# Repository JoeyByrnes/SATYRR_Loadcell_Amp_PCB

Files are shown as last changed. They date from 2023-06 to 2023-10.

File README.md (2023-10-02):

# SATYRR Loadcell Amplifier PCB
Loadcell Amplifiers for RoboDesign Lab SATYRR Wheeled-Humanoid robot

<p align="center">
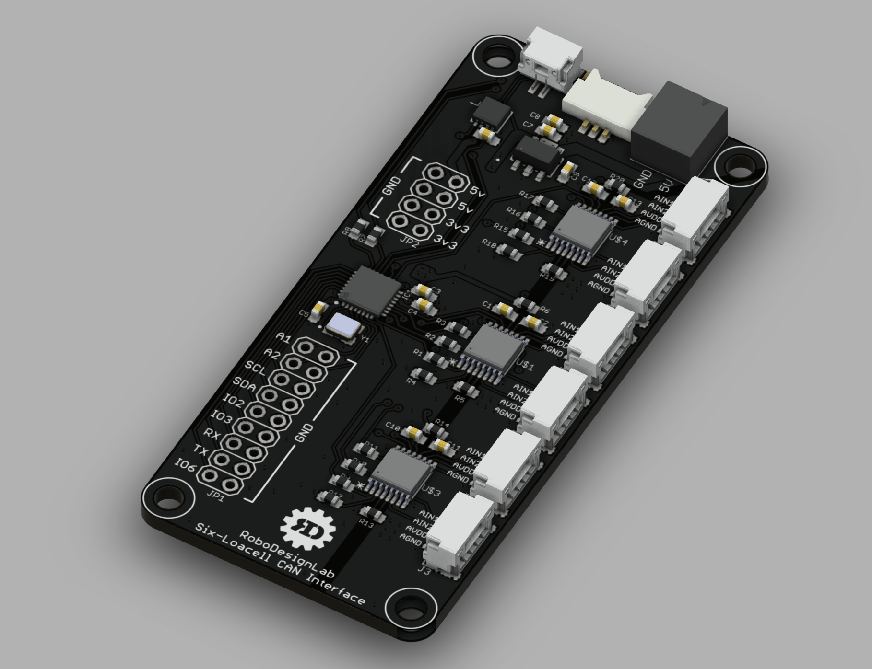
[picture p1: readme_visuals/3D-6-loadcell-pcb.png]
  
</p>

<p align="center">
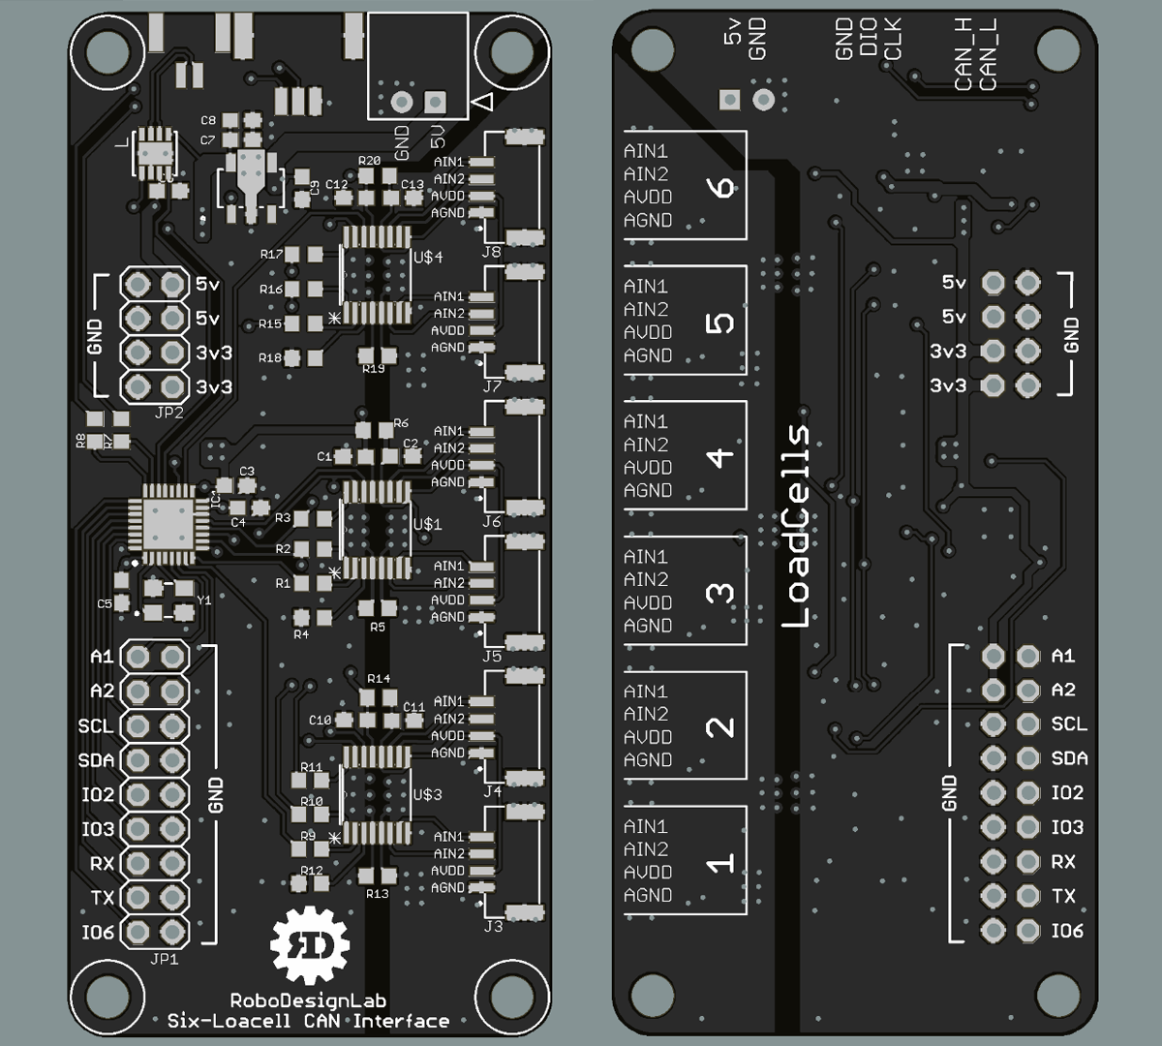
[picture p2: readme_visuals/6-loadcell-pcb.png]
  
</p>

<p align="center">
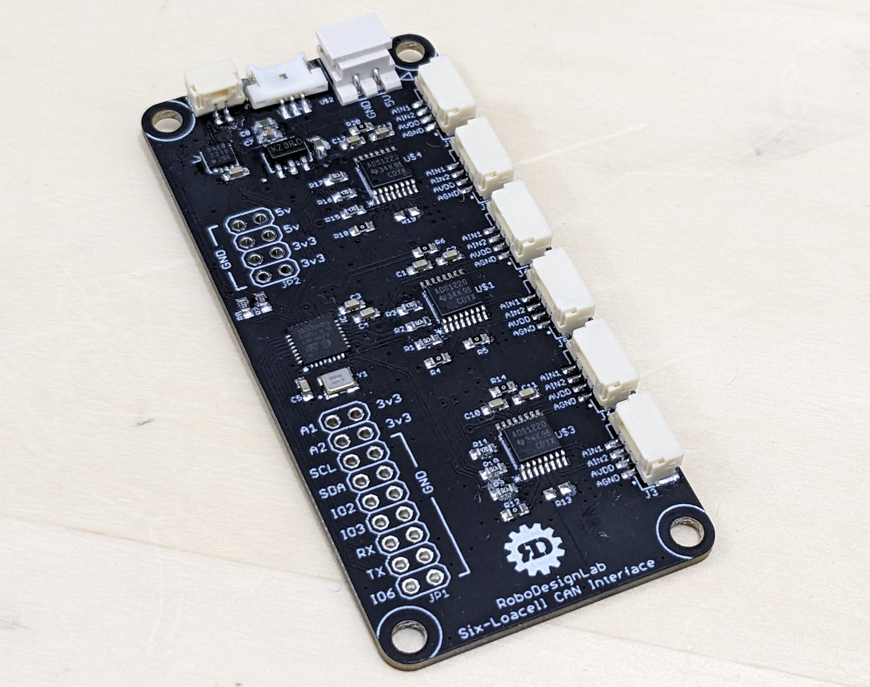
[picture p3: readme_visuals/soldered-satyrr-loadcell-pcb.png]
  
</p>

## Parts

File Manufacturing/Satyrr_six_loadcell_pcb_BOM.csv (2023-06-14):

Qty | Value | Package | Parts | Links
9 | 0R | R0603 | R4 R5 R6 R12 R13 R14 R18 R19 R20 | https://www.digikey.com/en/products/detail/stackpole-electronics-inc/RMCF0603ZT0R00/1756908
10 | 0.1uF | C0603 | C1 C2 C10 C11 C12 C13 C3 C4 C5 C6 | https://www.digikey.com/en/products/detail/samsung-electro-mechanics/CL10B104KB8NNWC/3887593
2 | 10uF | C0603 | C8 C9 | https://www.digikey.com/en/products/detail/taiyo-yuden/LMK107BBJ106MALT/3662195
1 | 125SH-G-03-TR-SMT | 125SH-G-03-TR-SMT | U$2 | https://www.digikey.com/en/products/detail/adam-tech/125SH-G-03-TR-SMT-T-R/10414814
1 | 22057025 | CON_22057025_MOL | J9 | https://www.digikey.com/en/products/detail/molex/0022057025/403341?s=N4IgTCBcDa5gDAVgOzzIkBdAvkA
2 | 22R | R0603 | R7 R8 | https://www.digikey.com/en/products/detail/te-connectivity-passive-product/CRGCQ0603J22R/8576683
1 | 4.7uF | C0603 | C7 | https://www.digikey.com/en/products/detail/taiyo-yuden/LMK107BJ475KAHT/4157765
9 | 47R | R0603 | R1 R2 R3 R9 R10 R11 R15 R16 R17 | https://www.digikey.com/en/products/detail/walsin-technology-corporation/WR06X470-JTL/13241762
3 | ADS1220 | TSSOP-16 | U$1 U$3 U$4 | https://www.mouser.com/ProductDetail/Texas-Instruments/ADS1220IPW?qs=5GI1giJCN%252BKzuruuF2dUlQ%3D%3D
1 | AP7361C-33Y5-13SOT89-5_DIO-M | SOT89-5_DIO-M | U2 | https://www.digikey.com/en/products/detail/diodes-incorporated/AP7361C-33Y5-13/5638323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
1 | ECS-80-18-33-JGN-TR | XTAL_ECS-240-8-33-AGN-TR | Y1 | https://www.digikey.com/en/products/detail/ecs-inc/ECS-80-18-33-JGN-TR/10478755
1 | MCP2562FD-H/MFDFN8_3X3MC_MCH-M | DFN8_3X3MC_MCH-M | U1 | https://www.newark.com/microchip/mcp2562fd-h-sn/can-transceiver-8mbps-40-to-150deg/dp/72AC6153?CMP=AFC-OP
1 | SM02BGHSTBLFSN | CONN_SM02BGHSTB_JST | J2 | https://www.digikey.com/en/products/detail/jst-sales-america-inc/SM02B-GHS-TB-LF-SN/807786
6 | SM04B-GHS-TB(LF)(SN)- | JST_SM04B-GHS-TB(LF)(SN)- | J3 J4 J5 J6 J7 J8 | https://www.digikey.com/en/products/detail/jst-sales-america-inc/SM04B-GHS-TB-LF-SN/807788
1 | STM32G431KBU6 | QFN50P500X500X60-33N | IC1 | https://www.digikey.com/en/products/detail/stmicroelectronics/STM32G431KBU6/10231568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

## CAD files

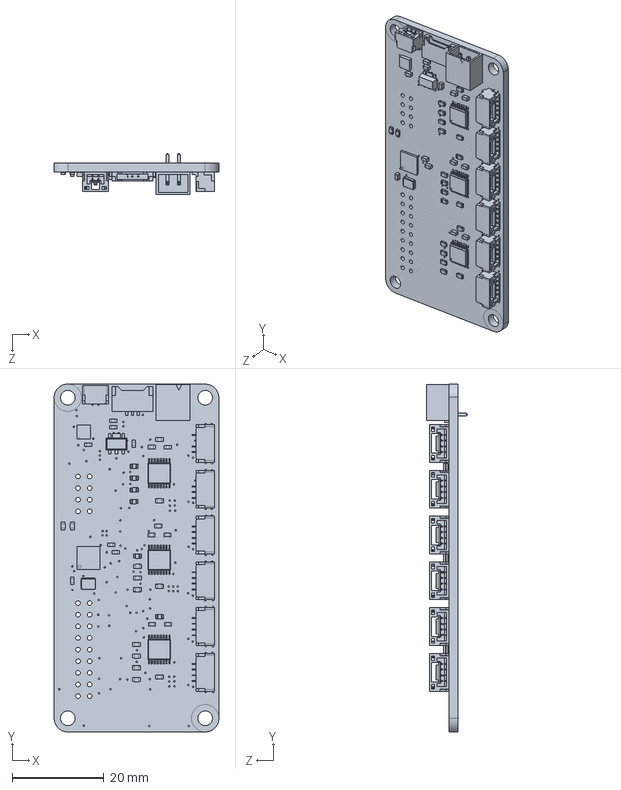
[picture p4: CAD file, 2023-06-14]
3D/Satyrr_6_loadcell_PCB.SLDPRT
36.0 x 76.0 x 9.00 mm

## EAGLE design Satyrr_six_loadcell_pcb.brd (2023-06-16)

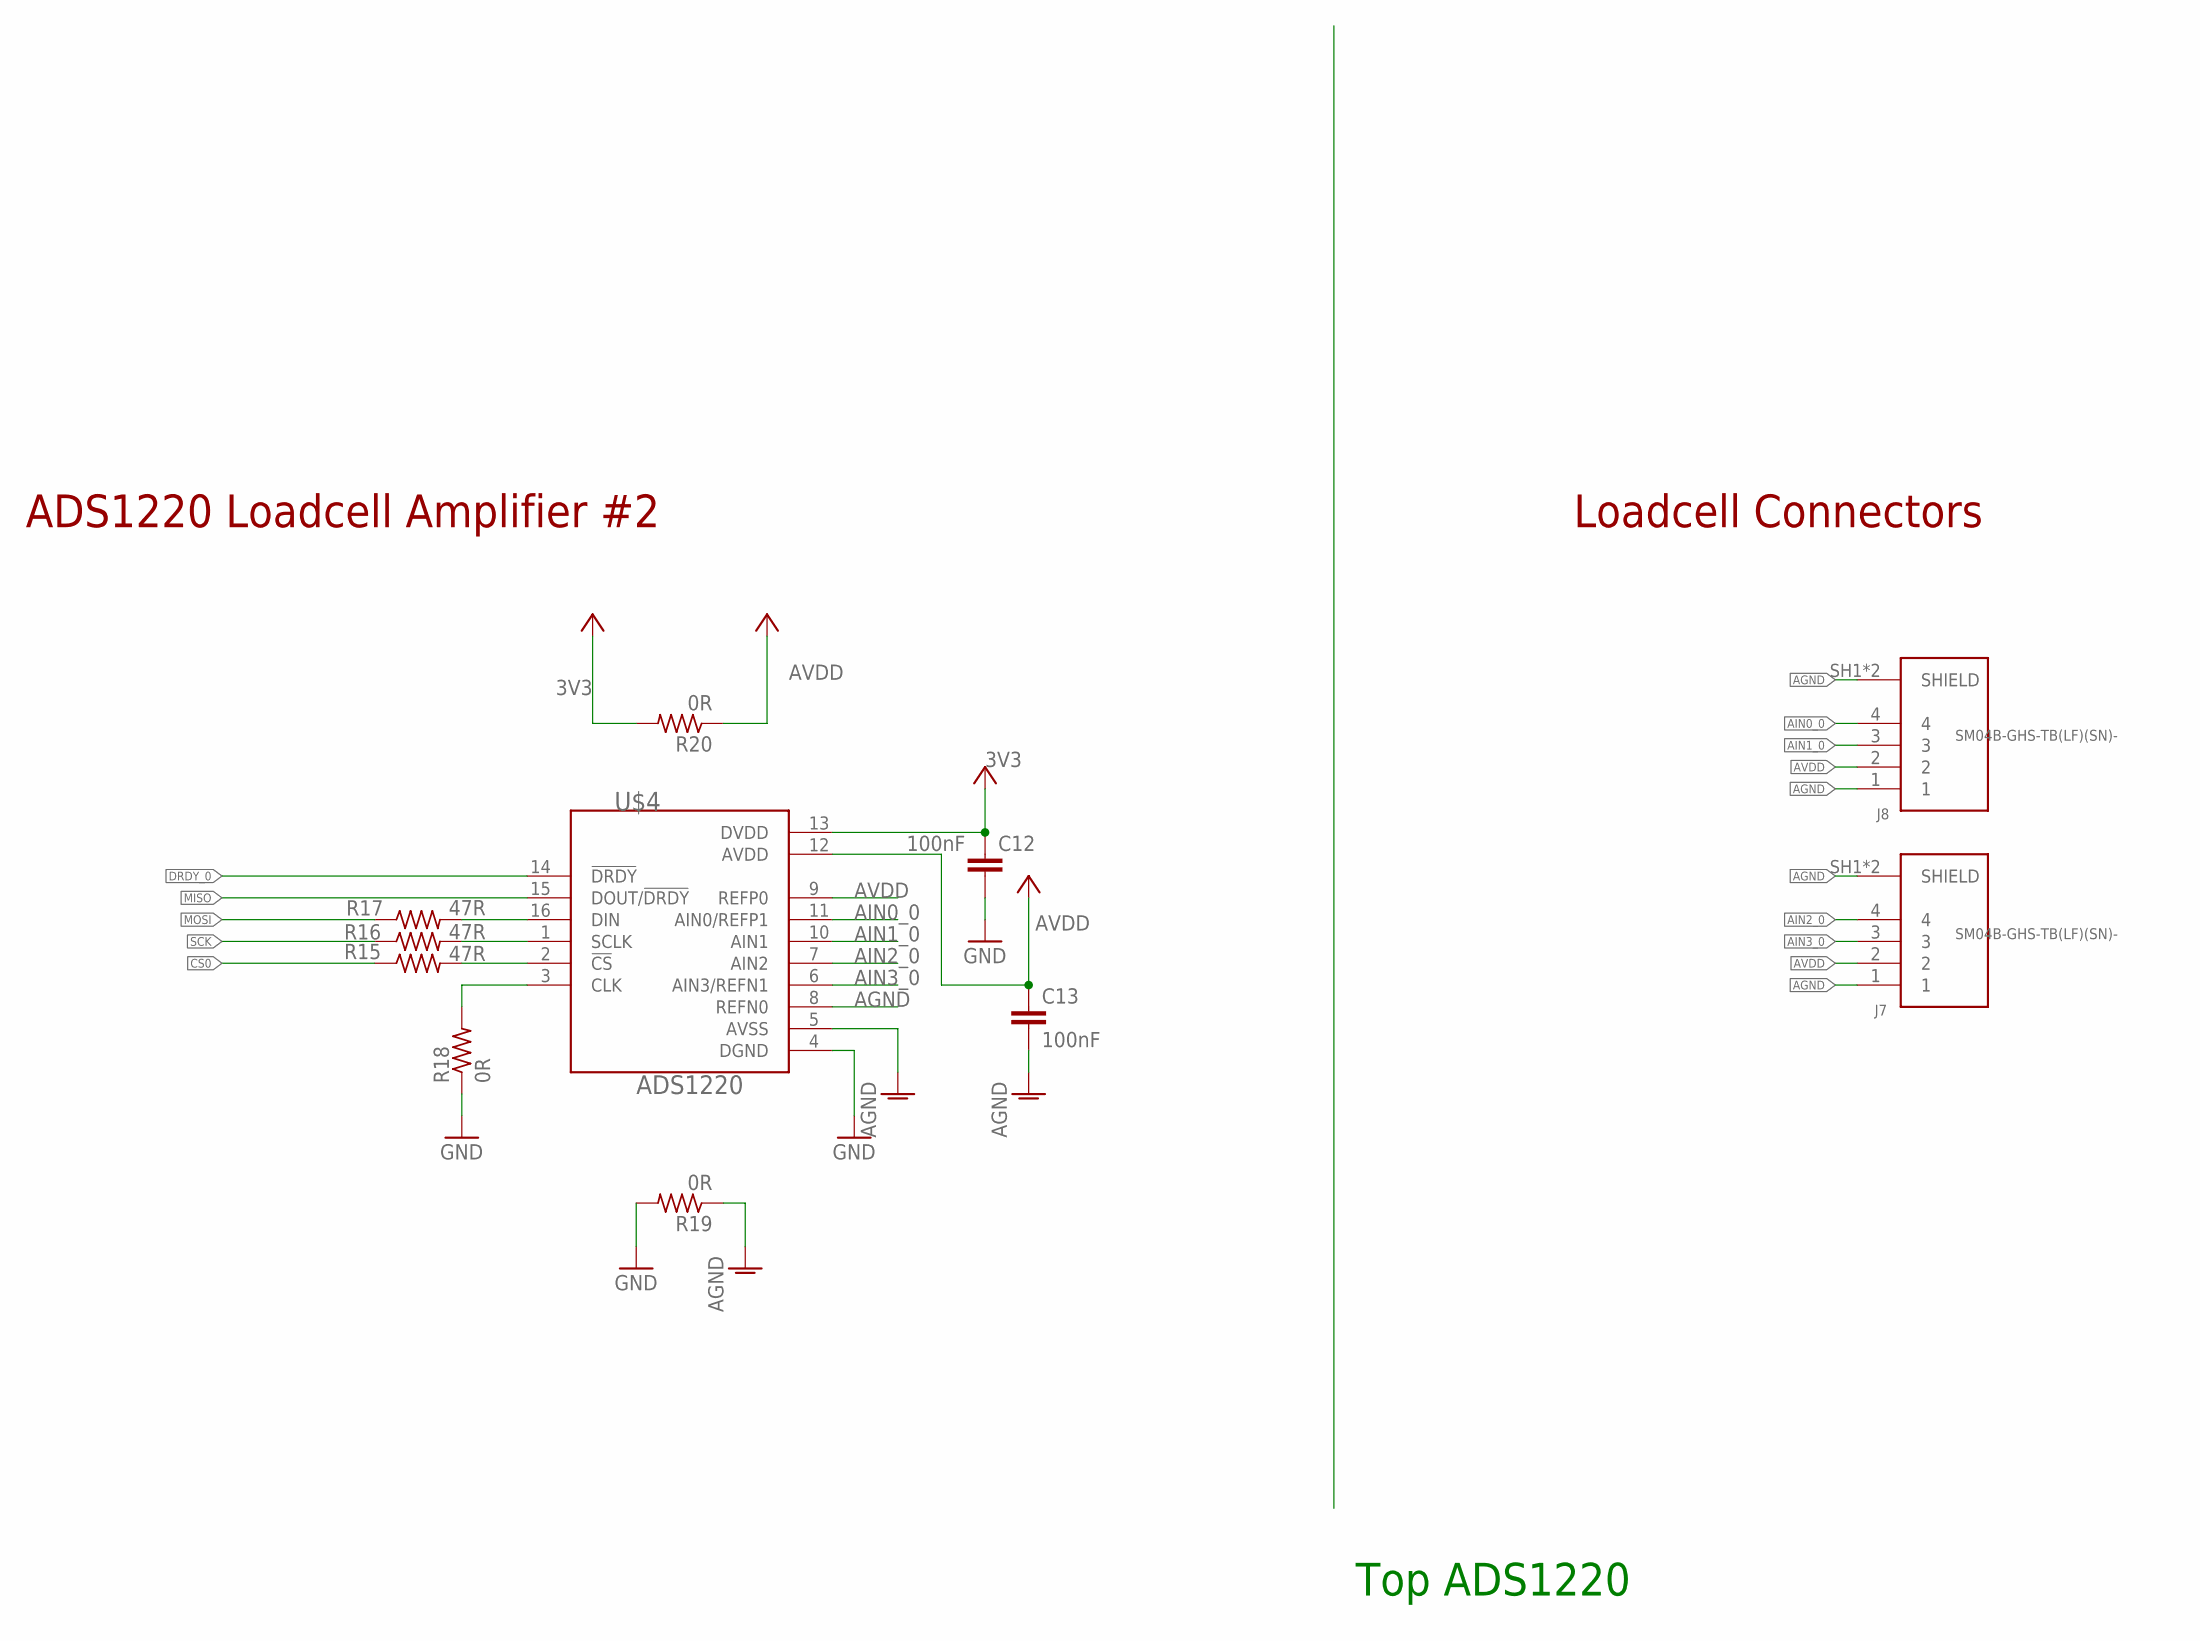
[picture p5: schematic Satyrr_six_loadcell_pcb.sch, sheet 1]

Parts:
C12, C13: 100nF; C0603
J7, J8: SM04B-GHS-TB(LF)(SN)-; JST_SM04B-GHS-TB(LF)(SN)-
R15, R16, R17: 47R; R0603
R18, R19, R20: 0R; R0603
U$4: ADS1220; TSSOP-16

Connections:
3V3: C12.1, R20.2, U$4.13 (DVDD); also elsewhere on the board
AGND: C13.2, J7.1, J7.SH1 (SHIELD), J7.SH2 (SHIELD), J8.1, J8.SH1 (SHIELD), J8.SH2 (SHIELD), R19.1, U$4.5 (AVSS), U$4.8 (REFN0); also elsewhere on the board
AIN0_0: J8.4, U$4.11 (AIN0/REFP1)
AIN1_0: J8.3, U$4.10 (AIN1)
AIN2_0: J7.4, U$4.7 (AIN2)
AIN3_0: J7.3, U$4.6 (AIN3/REFN1)
AVDD: C13.1, J7.2, J8.2, R20.1, U$4.9 (REFP0), U$4.12 (AVDD); also elsewhere on the board
CS0: R15.1; also elsewhere on the board
DRDY_0: U$4.14 (!DRDY); also elsewhere on the board
GND: C12.2, R18.1, R19.2, U$4.4 (DGND); also elsewhere on the board
MISO: U$4.15 (DOUT/!DRDY); also elsewhere on the board
MOSI: R17.1; also elsewhere on the board
unnamed: R17.2, U$4.16 (DIN)
unnamed: R16.2, U$4.1 (SCLK)
unnamed: R15.2, U$4.2 (!CS)
unnamed: R18.2, U$4.3 (CLK)
SCK: R16.1; also elsewhere on the board

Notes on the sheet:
Top ADS1220
ADS1220 Loadcell Amplifier #2
Loadcell Connectors

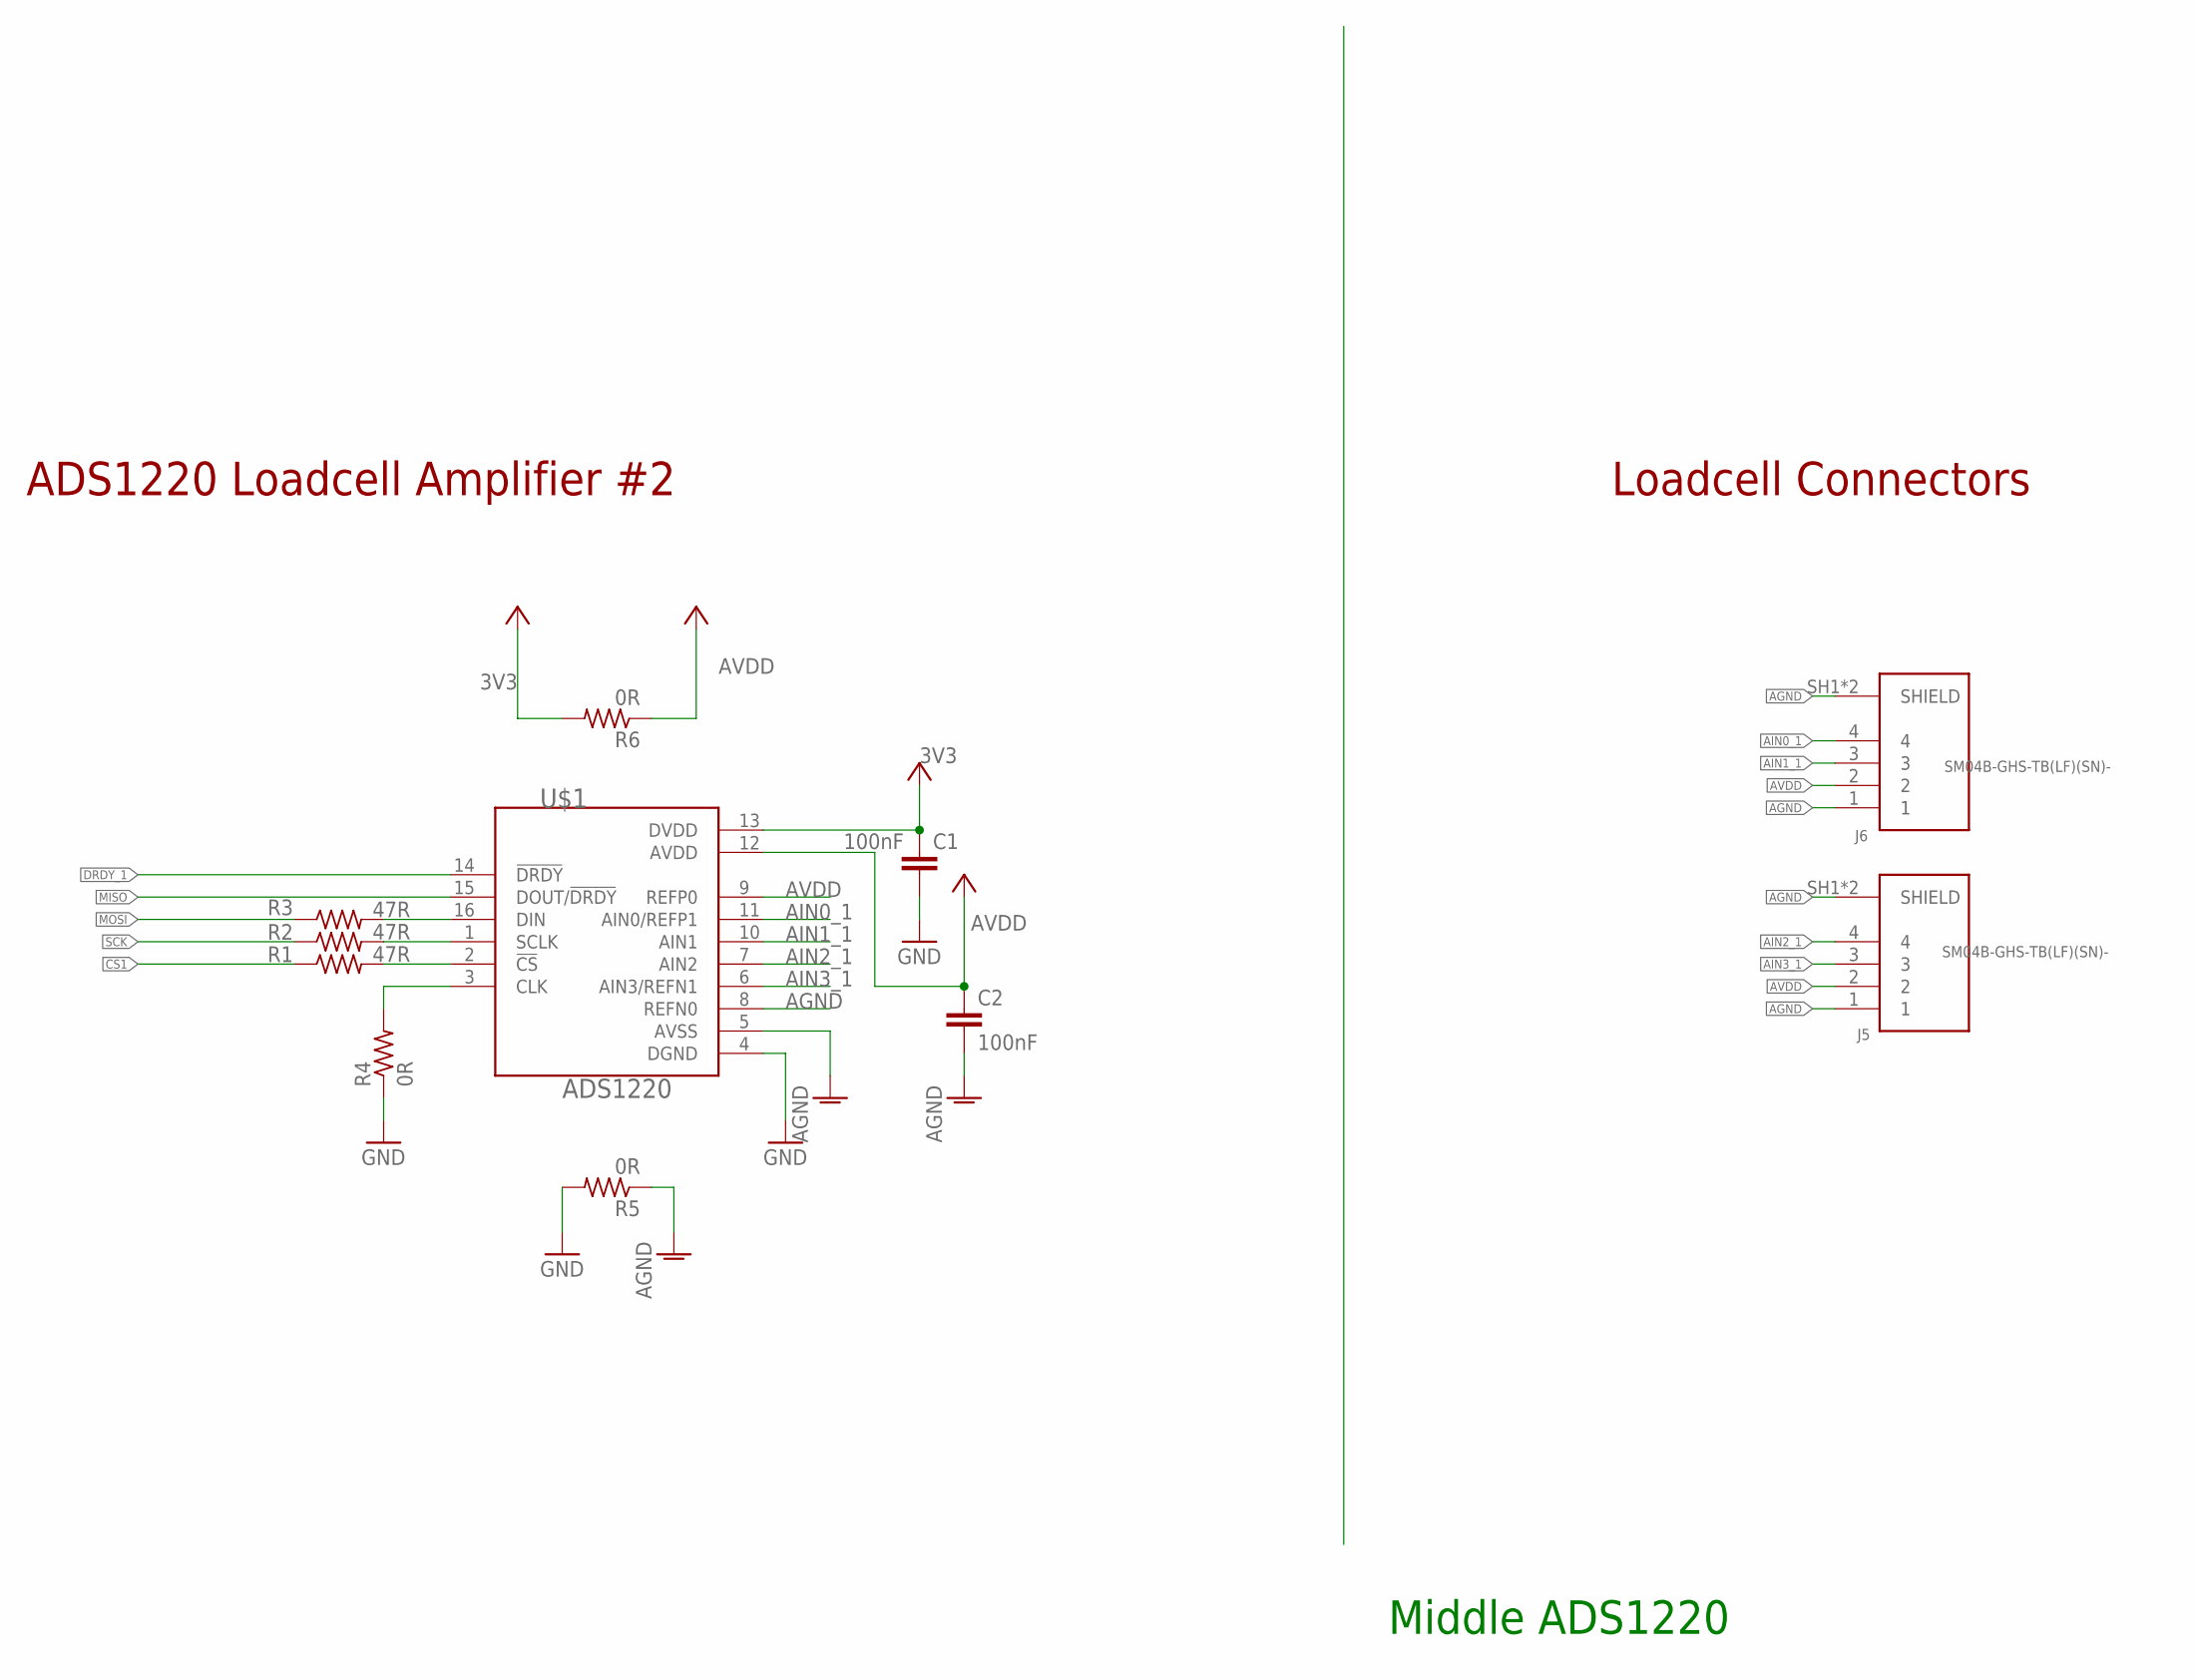
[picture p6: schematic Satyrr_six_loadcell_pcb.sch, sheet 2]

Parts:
C1, C2: 100nF; C0603
J5, J6: SM04B-GHS-TB(LF)(SN)-; JST_SM04B-GHS-TB(LF)(SN)-
R1, R2, R3: 47R; R0603
R4, R5, R6: 0R; R0603
U$1: ADS1220; TSSOP-16

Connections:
3V3: C1.1, R6.2, U$1.13 (DVDD); also elsewhere on the board
AGND: C2.2, J5.1, J5.SH1 (SHIELD), J5.SH2 (SHIELD), J6.1, J6.SH1 (SHIELD), J6.SH2 (SHIELD), R5.1, U$1.5 (AVSS), U$1.8 (REFN0); also elsewhere on the board
AIN0_1: J6.4, U$1.11 (AIN0/REFP1)
AIN1_1: J6.3, U$1.10 (AIN1)
AIN2_1: J5.4, U$1.7 (AIN2)
AIN3_1: J5.3, U$1.6 (AIN3/REFN1)
AVDD: C2.1, J5.2, J6.2, R6.1, U$1.9 (REFP0), U$1.12 (AVDD); also elsewhere on the board
CS1: R1.1; also elsewhere on the board
DRDY_1: U$1.14 (!DRDY); also elsewhere on the board
GND: C1.2, R4.1, R5.2, U$1.4 (DGND); also elsewhere on the board
MISO: U$1.15 (DOUT/!DRDY); also elsewhere on the board
MOSI: R3.1; also elsewhere on the board
unnamed: R3.2, U$1.16 (DIN)
unnamed: R2.2, U$1.1 (SCLK)
unnamed: R1.2, U$1.2 (!CS)
unnamed: R4.2, U$1.3 (CLK)
SCK: R2.1; also elsewhere on the board

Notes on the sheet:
Middle ADS1220
ADS1220 Loadcell Amplifier #2
Loadcell Connectors

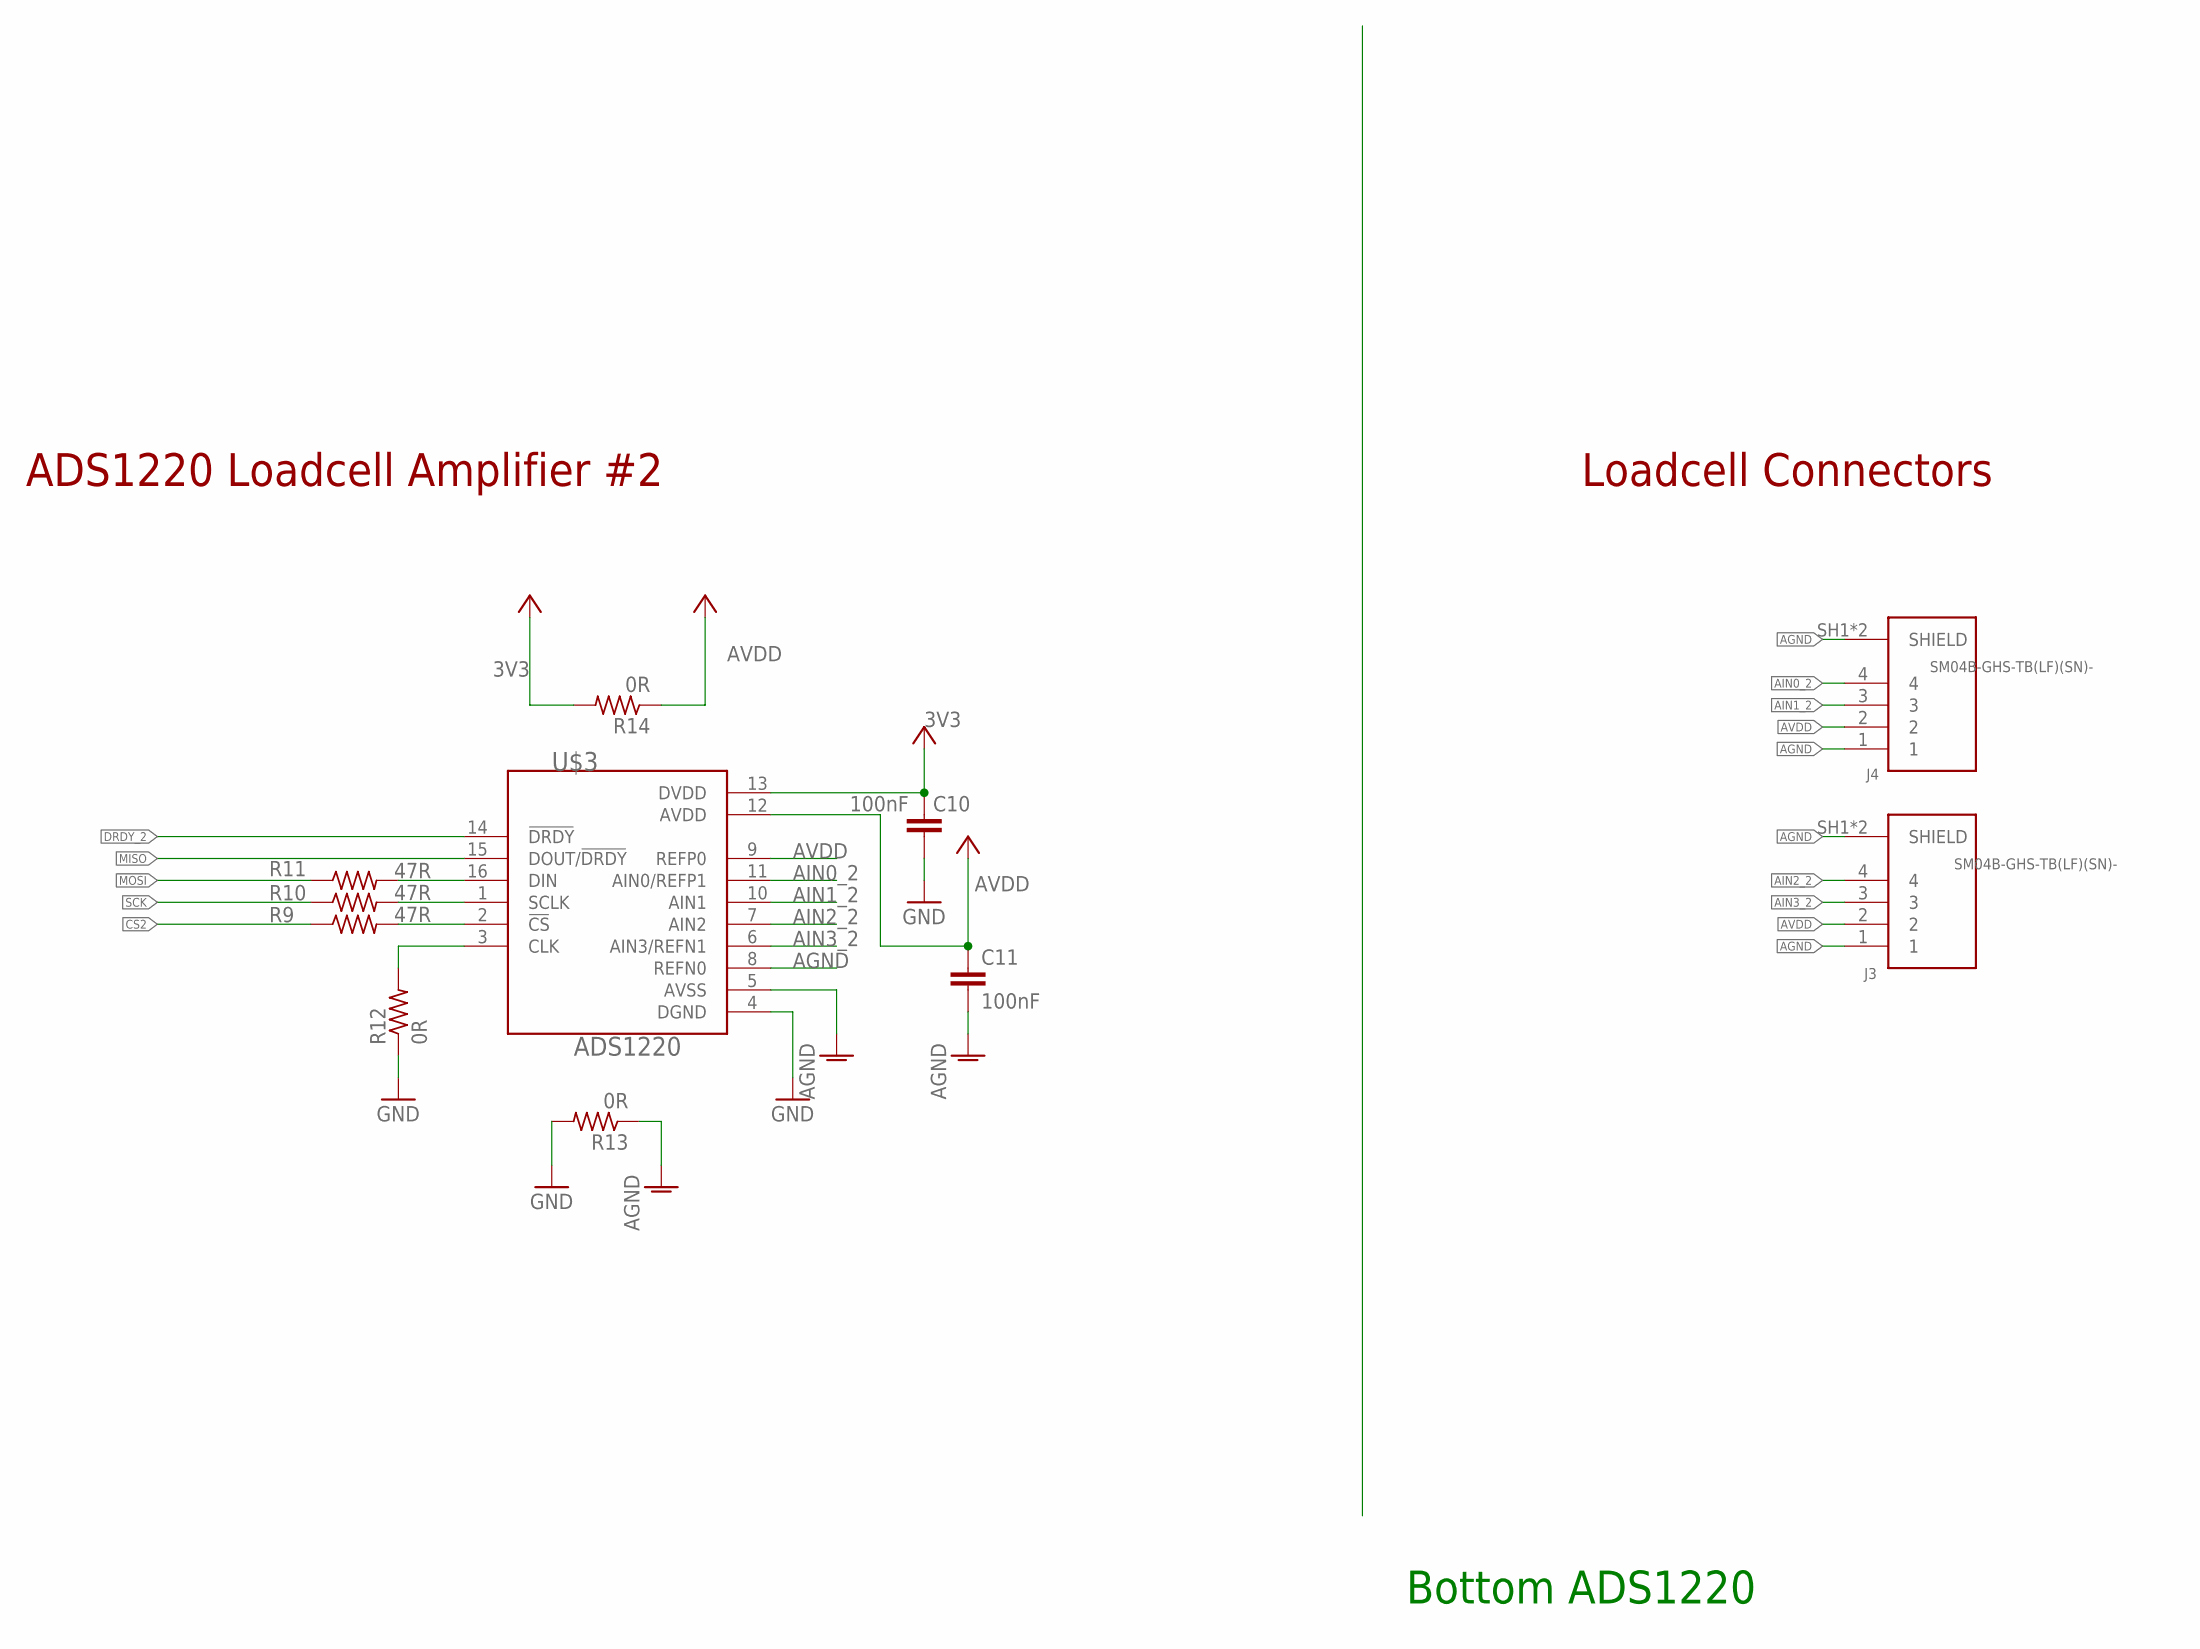
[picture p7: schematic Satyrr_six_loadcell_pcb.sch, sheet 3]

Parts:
C10, C11: 100nF; C0603
J3, J4: SM04B-GHS-TB(LF)(SN)-; JST_SM04B-GHS-TB(LF)(SN)-
R9, R10, R11: 47R; R0603
R12, R13, R14: 0R; R0603
U$3: ADS1220; TSSOP-16

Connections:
3V3: C10.1, R14.2, U$3.13 (DVDD); also elsewhere on the board
AGND: C11.2, J3.1, J3.SH1 (SHIELD), J3.SH2 (SHIELD), J4.1, J4.SH1 (SHIELD), J4.SH2 (SHIELD), R13.1, U$3.5 (AVSS), U$3.8 (REFN0); also elsewhere on the board
AIN0_2: J4.4, U$3.11 (AIN0/REFP1)
AIN1_2: J4.3, U$3.10 (AIN1)
AIN2_2: J3.4, U$3.7 (AIN2)
AIN3_2: J3.3, U$3.6 (AIN3/REFN1)
AVDD: C11.1, J3.2, J4.2, R14.1, U$3.9 (REFP0), U$3.12 (AVDD); also elsewhere on the board
CS2: R9.1; also elsewhere on the board
DRDY_2: U$3.14 (!DRDY); also elsewhere on the board
GND: C10.2, R12.1, R13.2, U$3.4 (DGND); also elsewhere on the board
MISO: U$3.15 (DOUT/!DRDY); also elsewhere on the board
MOSI: R11.1; also elsewhere on the board
unnamed: R11.2, U$3.16 (DIN)
unnamed: R10.2, U$3.1 (SCLK)
unnamed: R9.2, U$3.2 (!CS)
unnamed: R12.2, U$3.3 (CLK)
SCK: R10.1; also elsewhere on the board

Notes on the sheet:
Bottom ADS1220
ADS1220 Loadcell Amplifier #2
Loadcell Connectors

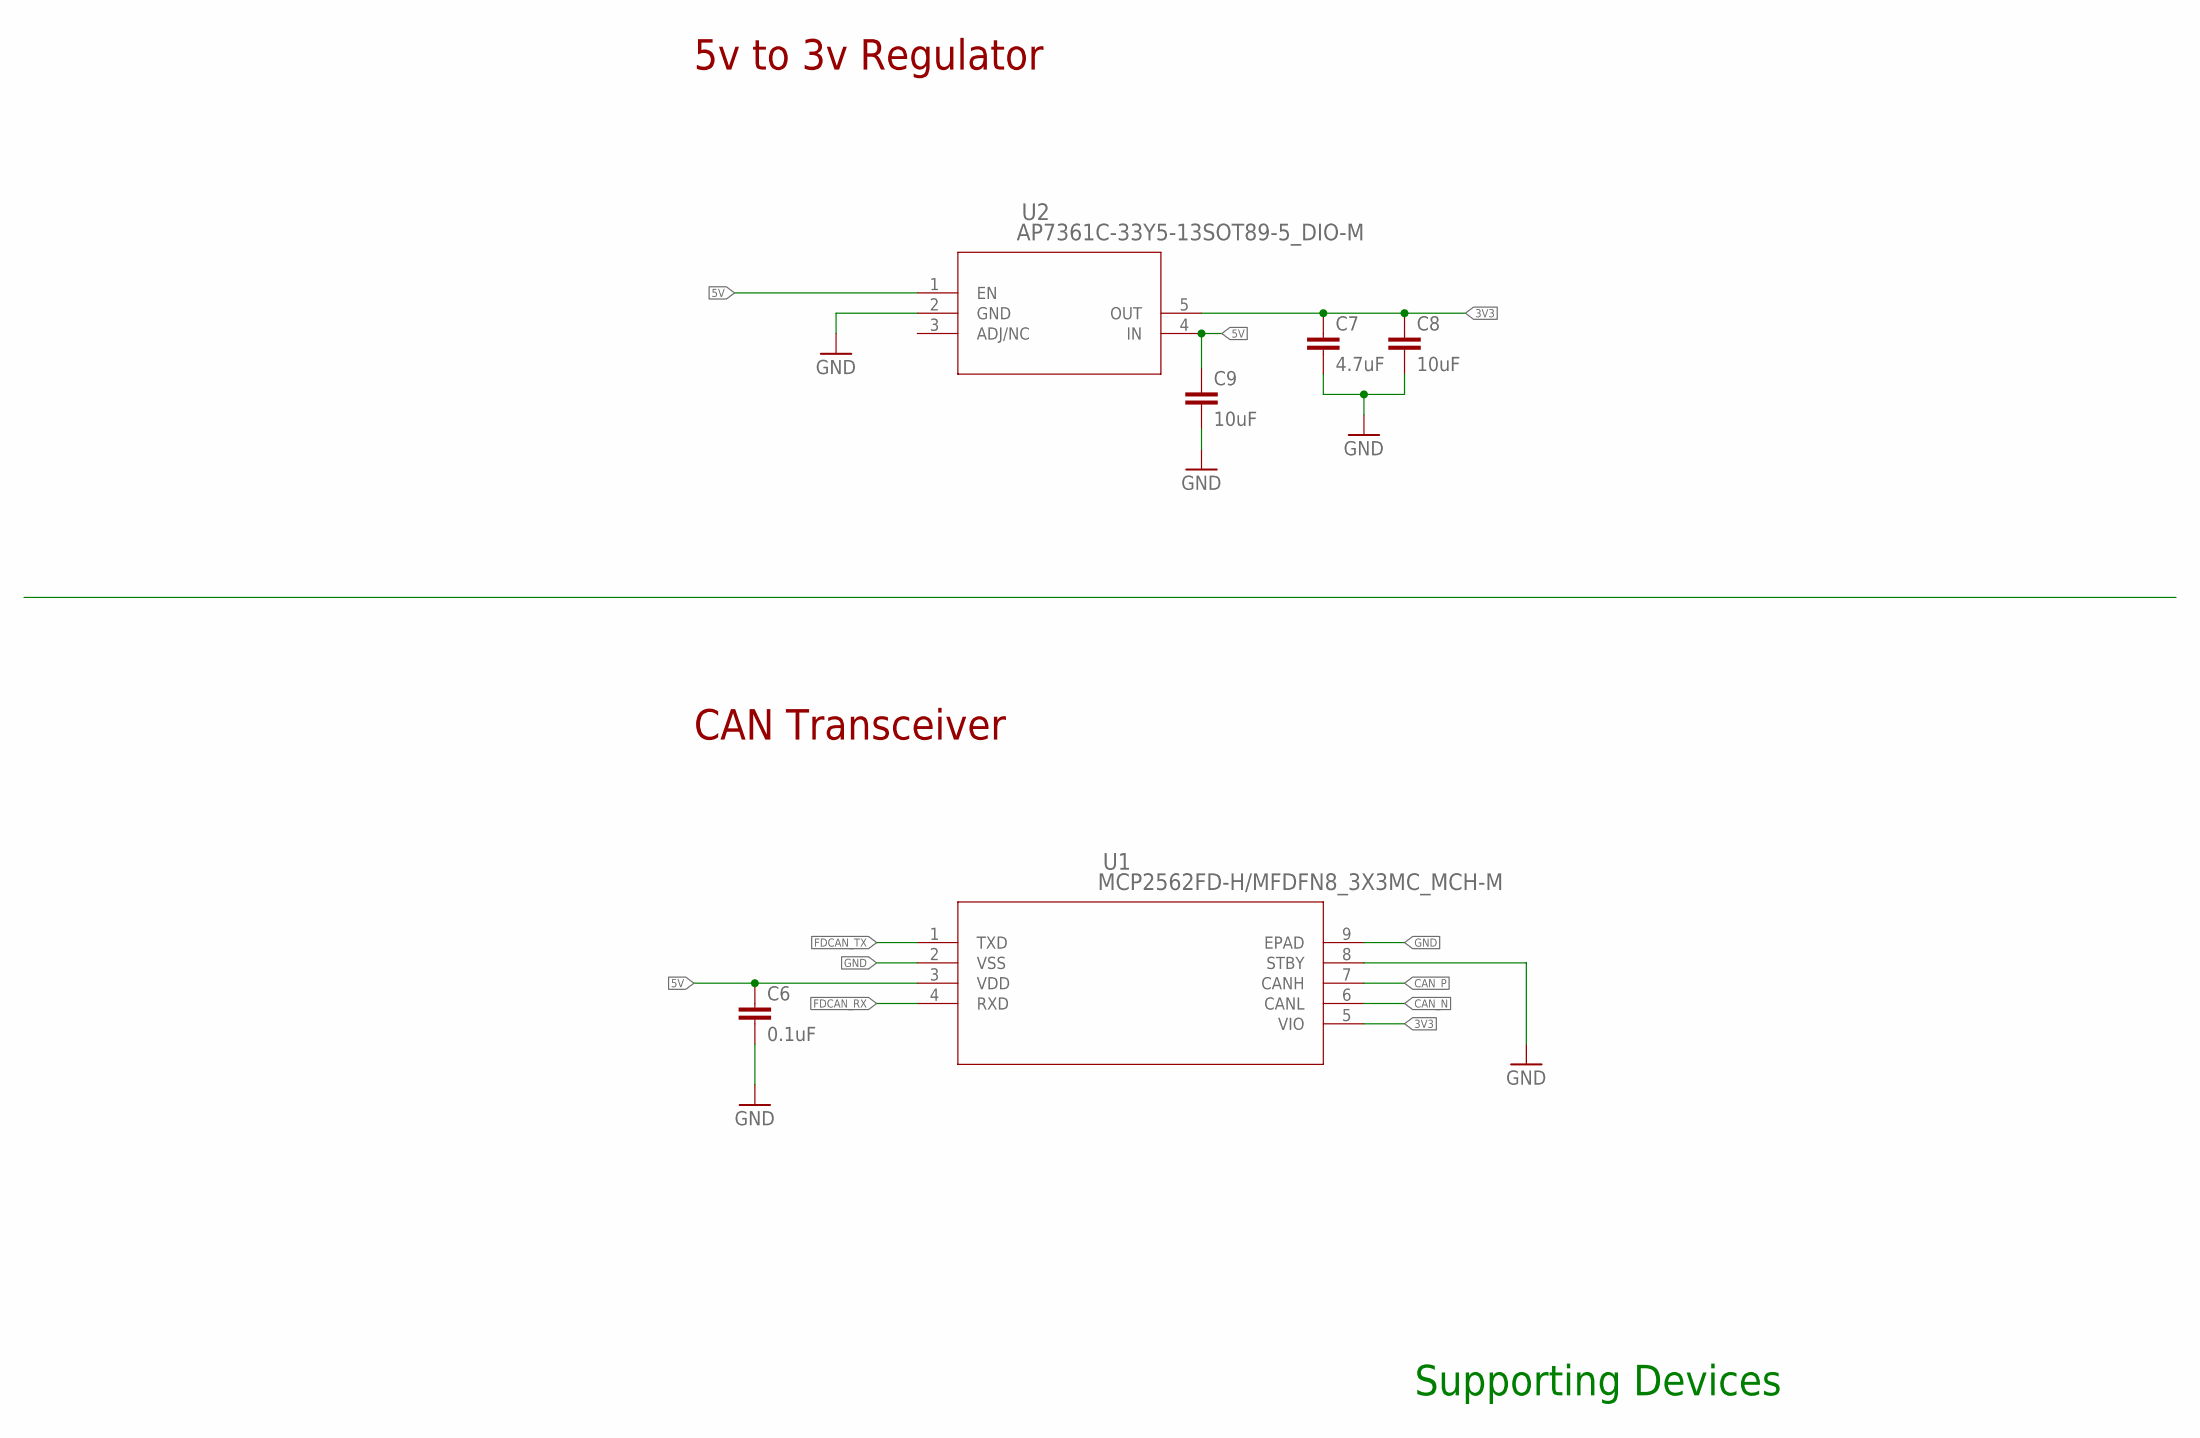
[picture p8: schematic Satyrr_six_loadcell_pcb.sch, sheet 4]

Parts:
C6: 0.1uF; C0603
C7: 4.7uF; C0603
C8, C9: 10uF; C0603
U1: MCP2562FD-H/MFDFN8_3X3MC_MCH-M; DFN8_3X3MC_MCH-M
U2: AP7361C-33Y5-13SOT89-5_DIO-M; SOT89-5_DIO-M

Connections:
3V3: C7.1, C8.1, U1.5 (VIO), U2.5 (OUT); also elsewhere on the board
5V: C6.1, C9.1, U1.3 (VDD), U2.1 (EN), U2.4 (IN); also elsewhere on the board
CAN_N: U1.6 (CANL); also elsewhere on the board
CAN_P: U1.7 (CANH); also elsewhere on the board
FDCAN_RX: U1.4 (RXD); also elsewhere on the board
FDCAN_TX: U1.1 (TXD); also elsewhere on the board
GND: C6.2, C7.2, C8.2, C9.2, U1.2 (VSS), U1.8 (STBY), U1.9 (EPAD), U2.2 (GND); also elsewhere on the board

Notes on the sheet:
5v to 3v Regulator
CAN Transceiver
Supporting Devices

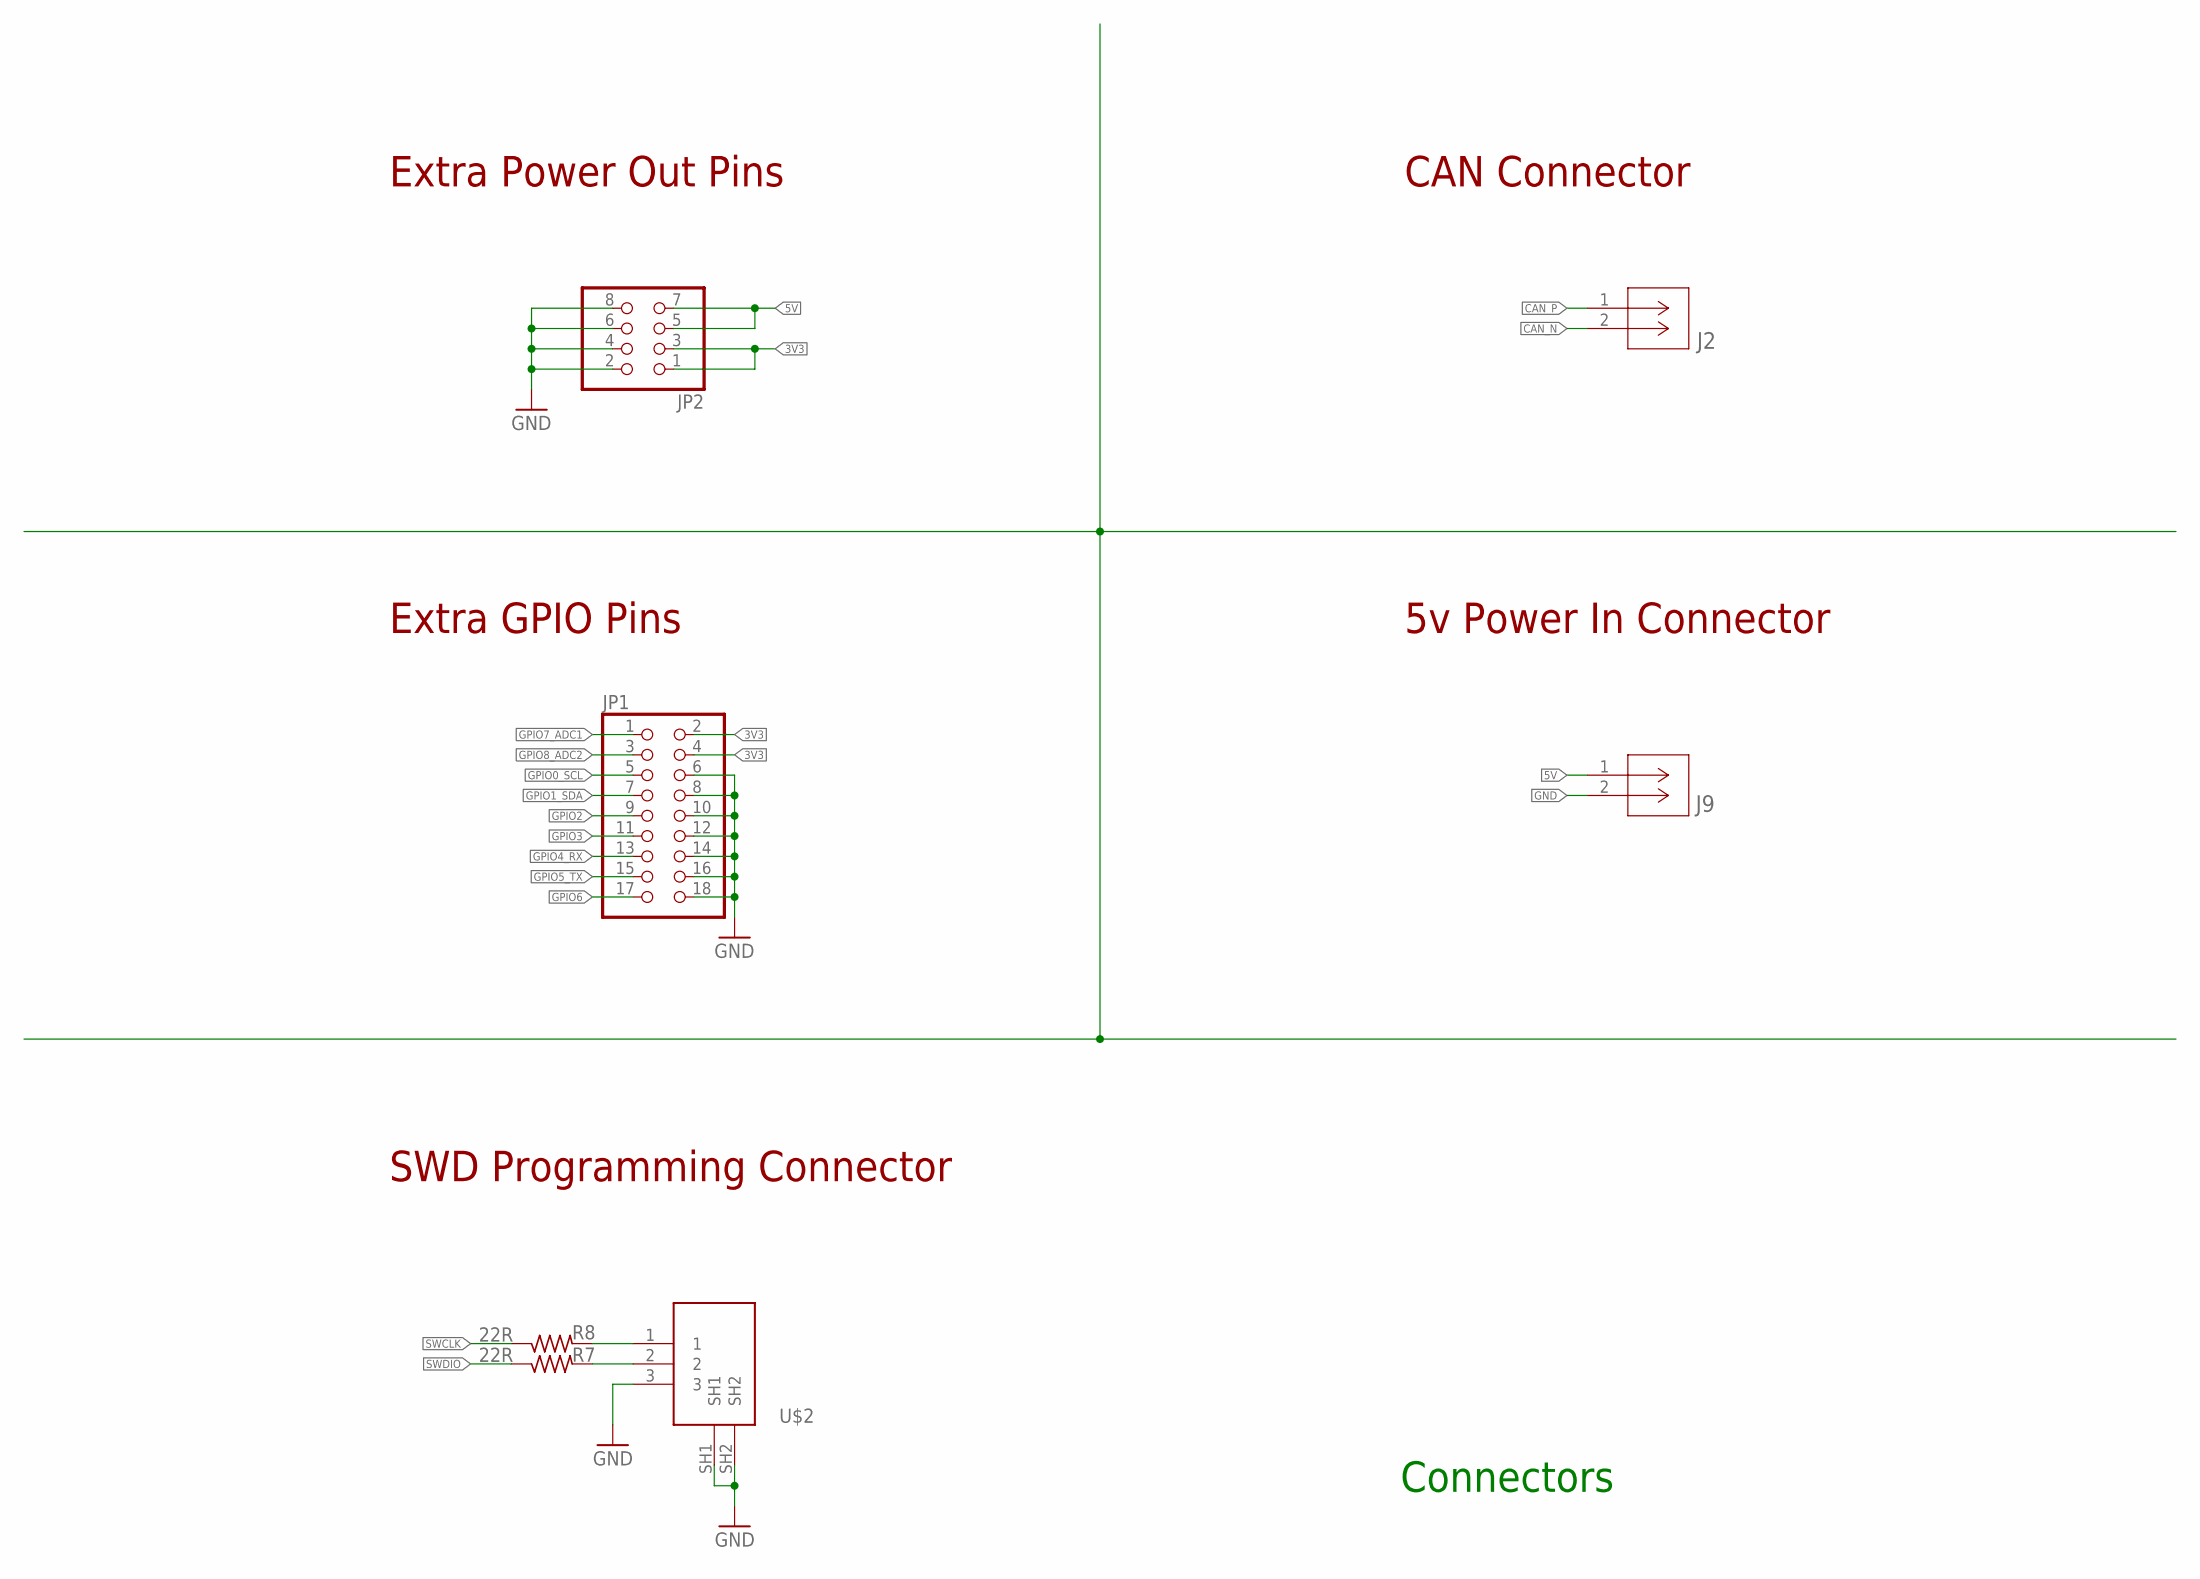
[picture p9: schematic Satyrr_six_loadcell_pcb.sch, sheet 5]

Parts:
J2: SM02BGHSTBLFSN; CONN_SM02BGHSTB_JST
J9: 22057025; CON_22057025_MOL
JP1: PINHD-2X9; 2X09
JP2: PINHD-2X4; 2X04
R7, R8: 22R; R0603
U$2: 125SH-G-03-TR-SMT

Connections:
3V3: JP1.2, JP1.4, JP2.1, JP2.3; also elsewhere on the board
5V: J9.1, JP2.5, JP2.7; also elsewhere on the board
CAN_N: J2.2; also elsewhere on the board
CAN_P: J2.1; also elsewhere on the board
GND: J9.2, JP1.6, JP1.8, JP1.10, JP1.12, JP1.14, JP1.16, JP1.18, JP2.2, JP2.4, JP2.6, JP2.8, U$2.3, U$2.SH1, U$2.SH2; also elsewhere on the board
GPIO0_SCL: JP1.5; also elsewhere on the board
GPIO1_SDA: JP1.7; also elsewhere on the board
GPIO2: JP1.9; also elsewhere on the board
GPIO3: JP1.11; also elsewhere on the board
GPIO4_RX: JP1.13; also elsewhere on the board
GPIO5_TX: JP1.15; also elsewhere on the board
GPIO6: JP1.17; also elsewhere on the board
GPIO7_ADC1: JP1.1; also elsewhere on the board
GPIO8_ADC2: JP1.3; also elsewhere on the board
SWCLK: R8.1; also elsewhere on the board
SWCLK_C: R8.2, U$2.1
SWDIO: R7.1; also elsewhere on the board
SWDIO_C: R7.2, U$2.2

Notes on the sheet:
U$2
Extra Power Out Pins
Extra GPIO Pins
CAN Connector
5v Power In Connector
SWD Programming Connector
Connectors

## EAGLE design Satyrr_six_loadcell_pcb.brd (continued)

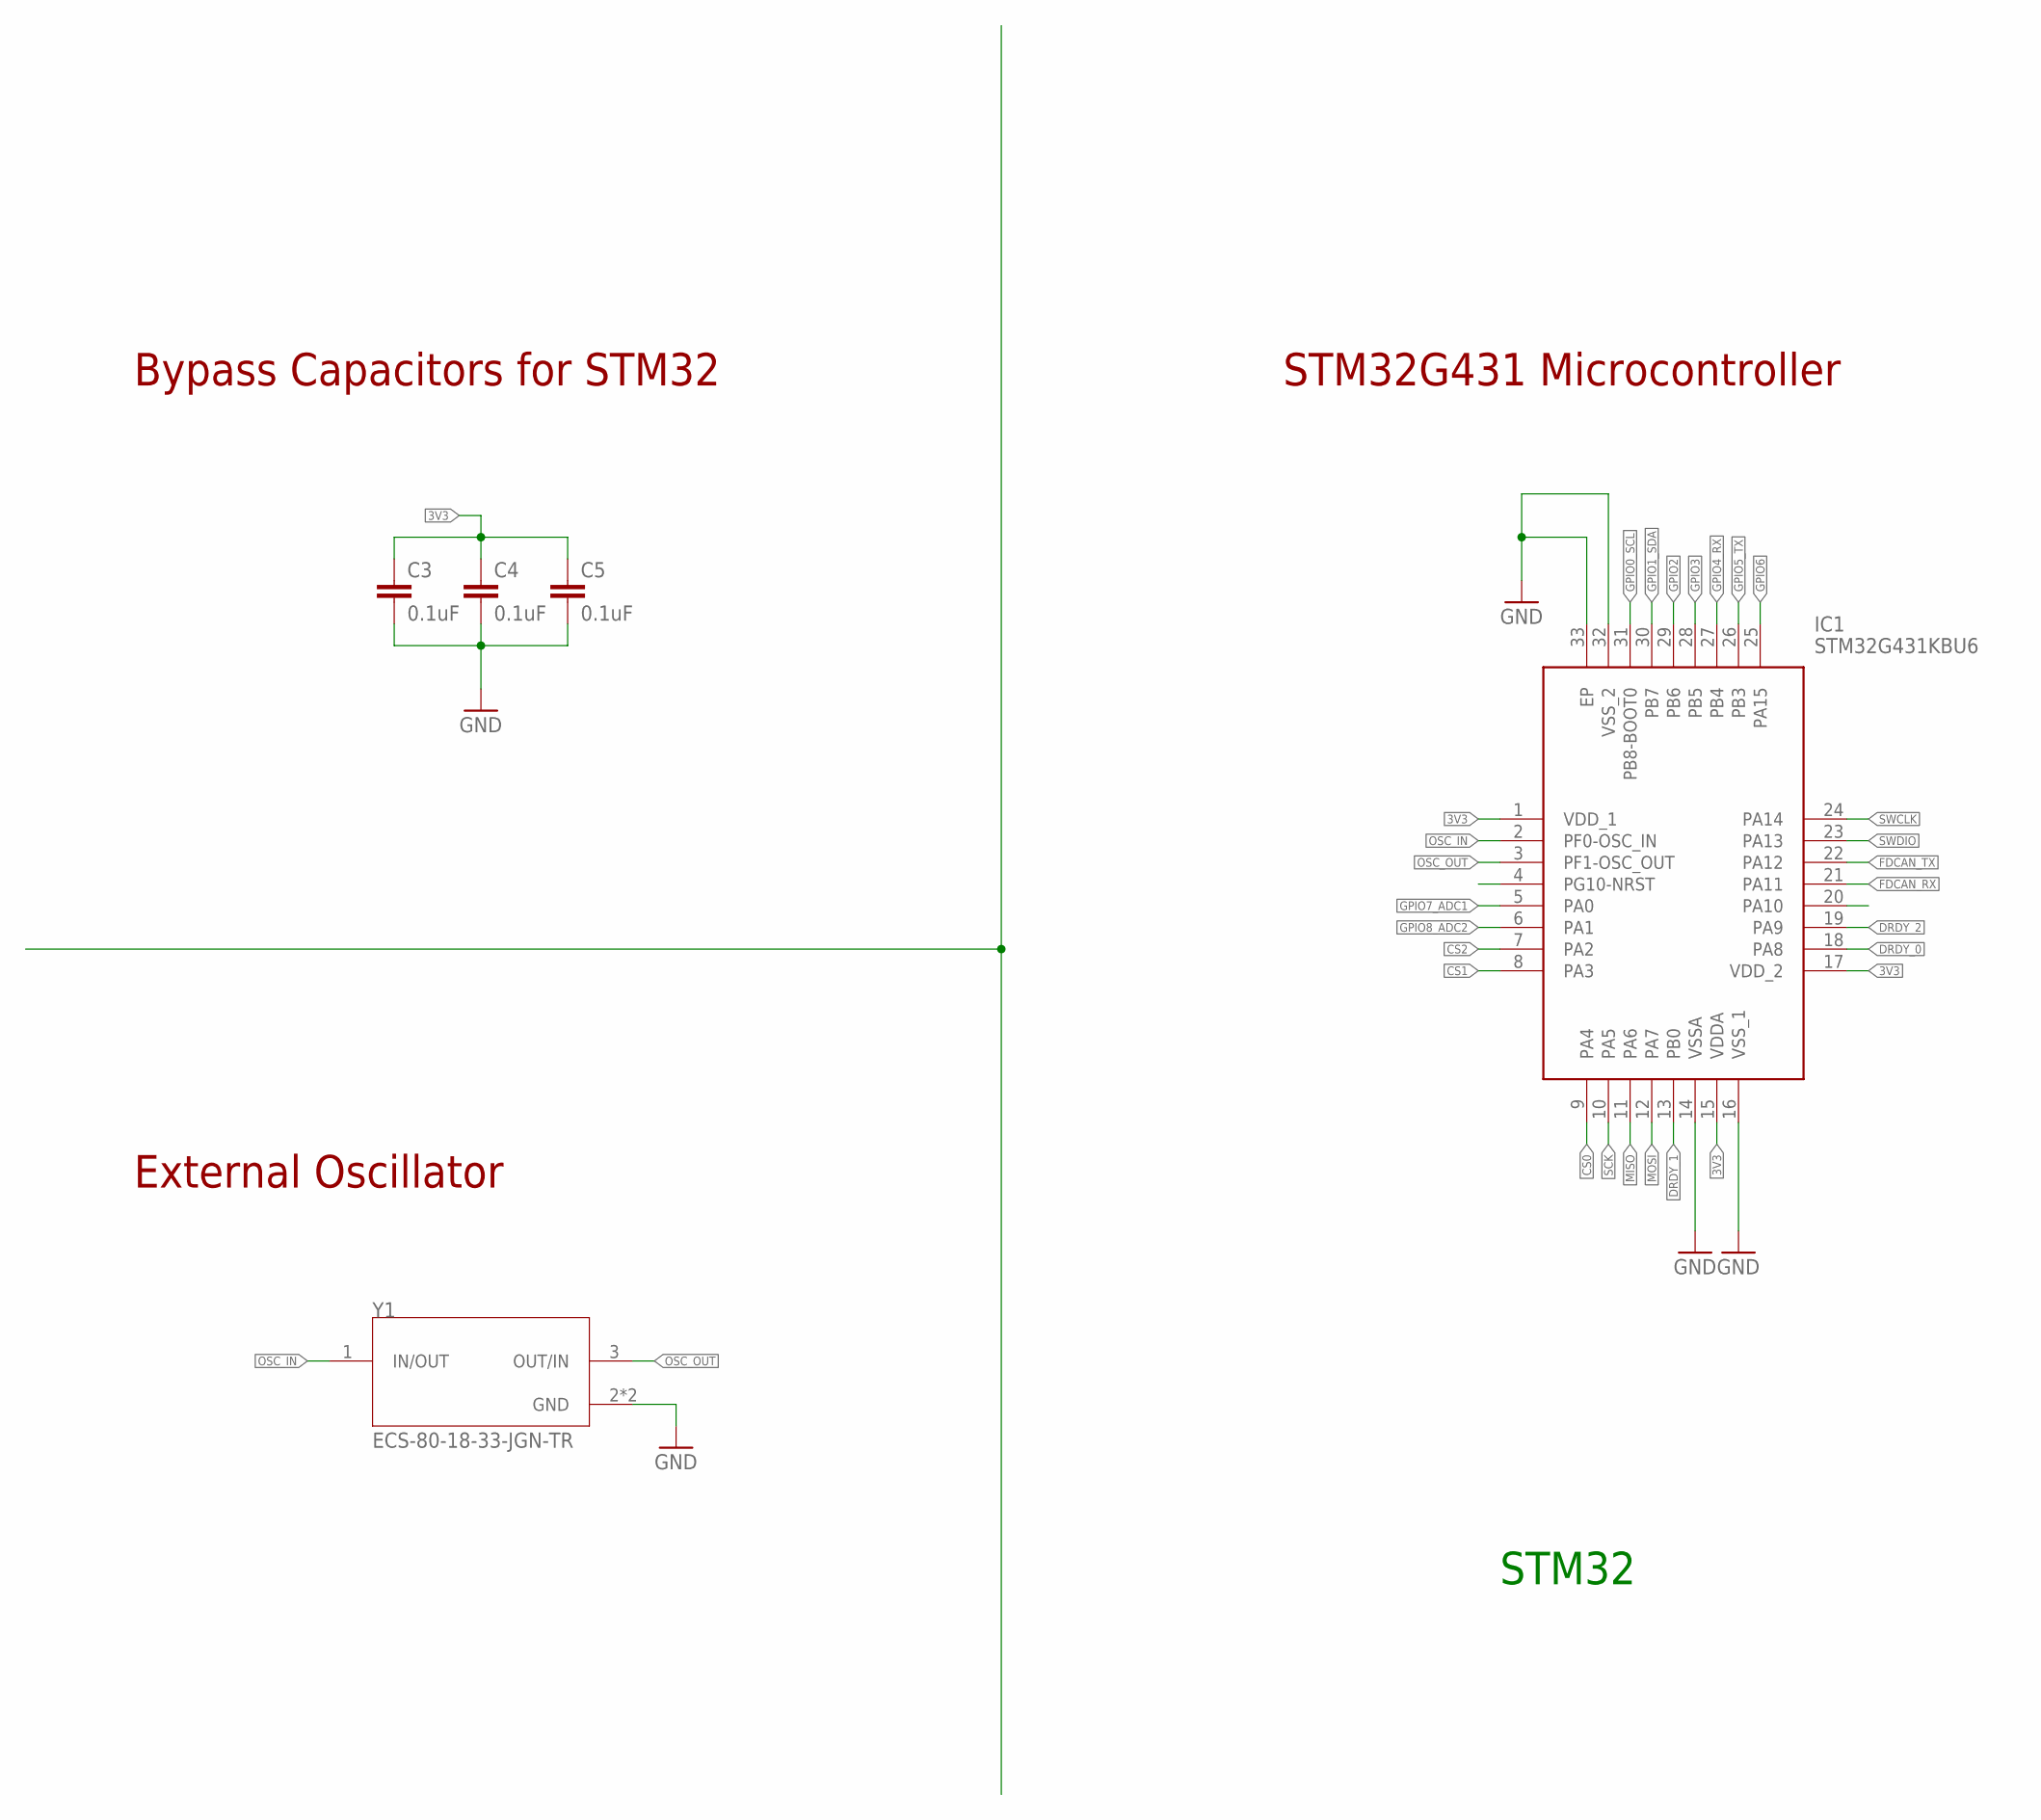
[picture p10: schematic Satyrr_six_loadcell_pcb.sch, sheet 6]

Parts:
C3, C4, C5: 0.1uF; C0603
IC1: STM32G431KBU6; QFN50P500X500X60-33N
Y1: ECS-80-18-33-JGN-TR; XTAL_ECS-240-8-33-AGN-TR

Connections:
3V3: C3.1, C4.1, C5.1, IC1.1 (VDD_1), IC1.15 (VDDA), IC1.17 (VDD_2); also elsewhere on the board
CS0: IC1.9 (PA4); also elsewhere on the board
CS1: IC1.8 (PA3); also elsewhere on the board
CS2: IC1.7 (PA2); also elsewhere on the board
DRDY_0: IC1.18 (PA8); also elsewhere on the board
DRDY_1: IC1.13 (PB0); also elsewhere on the board
DRDY_2: IC1.19 (PA9); also elsewhere on the board
FDCAN_RX: IC1.21 (PA11); also elsewhere on the board
FDCAN_TX: IC1.22 (PA12); also elsewhere on the board
GND: C3.2, C4.2, C5.2, IC1.14 (VSSA), IC1.16 (VSS_1), IC1.32 (VSS_2), IC1.33 (EP), Y1.2 (GND), Y1.4 (GND); also elsewhere on the board
GPIO0_SCL: IC1.31 (PB8-BOOT0); also elsewhere on the board
GPIO1_SDA: IC1.30 (PB7); also elsewhere on the board
GPIO2: IC1.29 (PB6); also elsewhere on the board
GPIO3: IC1.28 (PB5); also elsewhere on the board
GPIO4_RX: IC1.27 (PB4); also elsewhere on the board
GPIO5_TX: IC1.26 (PB3); also elsewhere on the board
GPIO6: IC1.25 (PA15); also elsewhere on the board
GPIO7_ADC1: IC1.5 (PA0); also elsewhere on the board
GPIO8_ADC2: IC1.6 (PA1); also elsewhere on the board
MISO: IC1.11 (PA6); also elsewhere on the board
MOSI: IC1.12 (PA7); also elsewhere on the board
OSC_IN: IC1.2 (PF0-OSC_IN), Y1.1 (IN/OUT)
OSC_OUT: IC1.3 (PF1-OSC_OUT), Y1.3 (OUT/IN)
SCK: IC1.10 (PA5); also elsewhere on the board
SWCLK: IC1.24 (PA14); also elsewhere on the board
SWDIO: IC1.23 (PA13); also elsewhere on the board

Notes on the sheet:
Bypass Capacitors for STM32
External Oscillator
STM32G431 Microcontroller
STM32

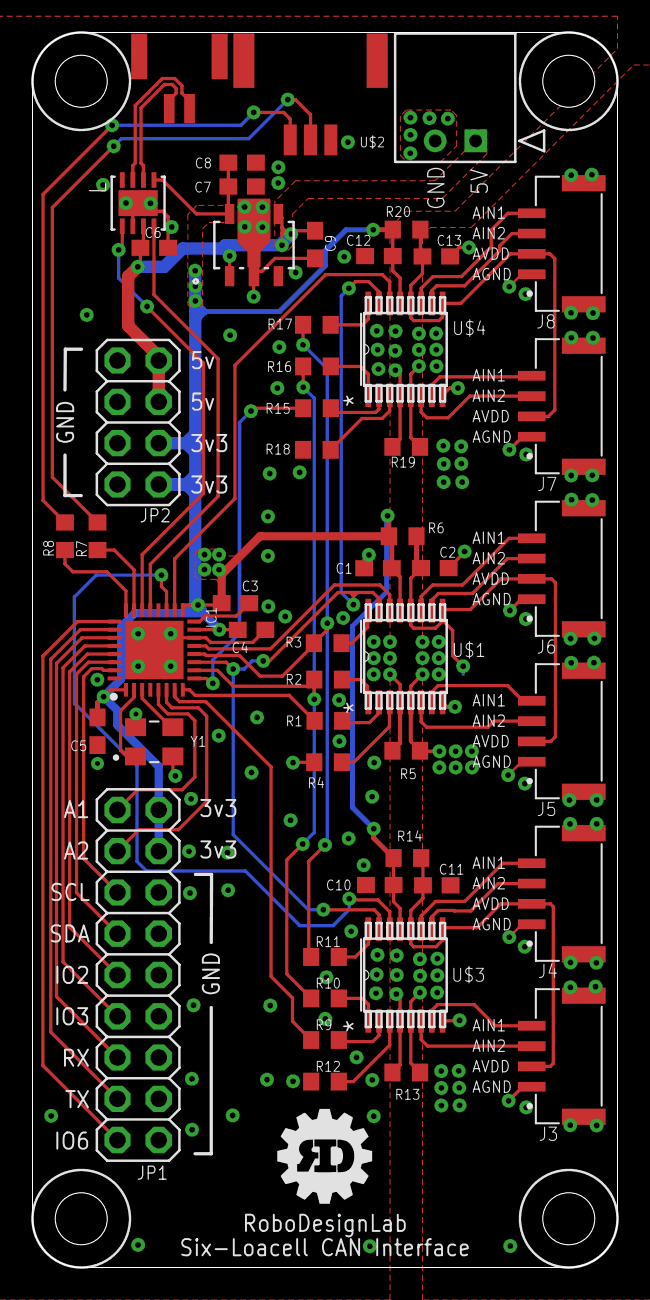
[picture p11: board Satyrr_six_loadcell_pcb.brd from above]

Board: 4 copper layers, 36.0 x 76.0 mm, 51 parts (0 on the bottom side), 57 nets.

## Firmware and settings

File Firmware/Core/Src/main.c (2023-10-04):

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
/* Includes ------------------------------------------------------------------*/
#include "main.h"
#include "adc.h"
#include "fdcan.h"
#include "spi.h"
#include "tim.h"
#include "usart.h"
#include "gpio.h"


void SystemClock_Config(void);
/* USER CODE BEGIN 0 */

void usleep(uint32_t us)
{
    // Clock cycles per microsecond for a 170MHz clock
    const uint32_t CYCLES_PER_MICROSECOND = 13; // ---> 170/13 (~13 clock cycles per operation)

    uint32_t totalCycles = us * CYCLES_PER_MICROSECOND;

    // Loop to execute the NOP instruction for the desired delay
    for (uint32_t i = 0; i < totalCycles; ++i)
    {
        asm volatile("NOP");
    }
}

/* USER CODE END 0 */

/**
  * @brief  The application entry point.
  * @retval int
  */
int main(void)
{
  /* MCU Configuration--------------------------------------------------------*/

  /* Reset of all peripherals, Initializes the Flash interface and the Systick. */
  HAL_Init();

  /* Configure the system clock */
  SystemClock_Config();

  /* USER CODE BEGIN SysInit */
  HAL_Delay(2000);
  /* USER CODE END SysInit */

  /* Initialize all configured peripherals */
  MX_GPIO_Init();
  MX_FDCAN1_Init();
  MX_SPI1_Init();
  MX_TIM2_Init();
  MX_ADC1_Init();
  MX_TIM1_Init();
  MX_USART2_UART_Init();
  /* USER CODE BEGIN 2 */

//  DWT_Init();

  // Enable GPIOB clock
  __HAL_RCC_GPIOA_CLK_ENABLE();
  __HAL_RCC_GPIOB_CLK_ENABLE();

  // Configure PB6 as output
  GPIO_InitTypeDef GPIO_InitStruct;
  GPIO_InitStruct.Pin = GPIO_PIN_5 | GPIO_PIN_6;
  GPIO_InitStruct.Mode = GPIO_MODE_OUTPUT_PP;
  GPIO_InitStruct.Pull = GPIO_NOPULL;
  GPIO_InitStruct.Speed = GPIO_SPEED_FREQ_HIGH;
  HAL_GPIO_Init(GPIOB, &GPIO_InitStruct);

  // Set chip selects as outputs and initialize them to high
  GPIO_InitTypeDef GPIO_InitStruct2 = {0};
  GPIO_InitStruct2.Pin = GPIO_PIN_2 | GPIO_PIN_3 | GPIO_PIN_4;
  GPIO_InitStruct2.Mode = GPIO_MODE_OUTPUT_PP;
  GPIO_InitStruct2.Pull = GPIO_NOPULL;
  GPIO_InitStruct2.Speed = GPIO_SPEED_FREQ_HIGH;
  HAL_GPIO_Init(GPIOA, &GPIO_InitStruct2);

  // GPIOA Pin 9 (PA9) configuration as input
  GPIO_InitTypeDef GPIO_InitStruct3;
  GPIO_InitStruct3.Pin = GPIO_PIN_9;
  GPIO_InitStruct3.Mode = GPIO_MODE_INPUT;
  GPIO_InitStruct3.Pull = GPIO_NOPULL;
  HAL_GPIO_Init(GPIOA, &GPIO_InitStruct3);

  // GPIOA Pin 8 (PA8) configuration as input
  GPIO_InitStruct3.Pin = GPIO_PIN_8;
  HAL_GPIO_Init(GPIOA, &GPIO_InitStruct3);

  // GPIOB Pin 0 (PB0) configuration as input
  GPIO_InitStruct3.Pin = GPIO_PIN_0;
  HAL_GPIO_Init(GPIOB, &GPIO_InitStruct3);

  // Initialize chip selects to high
  HAL_GPIO_WritePin(GPIOA, GPIO_PIN_2, GPIO_PIN_SET);
  HAL_GPIO_WritePin(GPIOA, GPIO_PIN_3, GPIO_PIN_SET);
  HAL_GPIO_WritePin(GPIOA, GPIO_PIN_4, GPIO_PIN_SET);

  HAL_FDCAN_Start(&hfdcan1);
  // Start Timer 1
//

  /* USER CODE END 2 */

  /* Infinite loop */
  /* USER CODE BEGIN WHILE */
  char message[] = "LoadCell Program Started.\r\n";
  HAL_UART_Transmit(&huart2, (uint8_t *)message, strlen(message),1);
  alt_main();

  while (1)
  {

    /* USER CODE END WHILE */

    /* USER CODE BEGIN 3 */
  }
  /* USER CODE END 3 */
}

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


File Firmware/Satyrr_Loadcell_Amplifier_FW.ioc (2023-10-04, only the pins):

Mcu.UserName=STM32G431KBUx
PA0.Signal=ADC1_IN1
PA1.Signal=ADC1_IN2
PA11.Signal=FDCAN1_RX
PA12.Signal=FDCAN1_TX
PA13.Signal=SYS_JTMS-SWDIO
PA14.Signal=SYS_JTCK-SWCLK
PA15.Signal=GPIO_Output
PA2.Signal=GPIO_Output
PA3.Signal=GPIO_Output
PA4.Signal=GPIO_Output
PA5.Signal=SPI1_SCK
PA6.Signal=SPI1_MISO
PA7.Signal=SPI1_MOSI
PA8.Signal=GPIO_Input
PA9.Signal=GPIO_Input
PB0.Signal=GPIO_Input
PB3.Signal=USART2_TX
PB4.Signal=USART2_RX
PB5.Signal=GPIO_Output
PB6.Signal=GPIO_Output
PB7.Signal=I2C1_SDA
PB8-BOOT0.Signal=I2C1_SCL
PF0-OSC_IN.Signal=RCC_OSC_IN
PF1-OSC_OUT.Signal=RCC_OSC_OUT

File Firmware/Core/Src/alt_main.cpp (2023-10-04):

#include <dwt_delay.hpp>
#include "alt_main.h"
#include "stm32g4xx_hal.h"
#include <Protocentral_ADS1220.hpp>
#include <string.h>
#include <stdio.h>
#include "main.h"

#define PGA 32                // Programmable Gain, confirm that the same as set_pga_gain
#define VREF 2.048            // Internal reference of 2.048V
#define VFSR VREF/PGA
#define FSR (((long int)1<<23)-1)

#define CAN_DEVICE_ID (uint8_t)20
#define CAN_MASTER_ID (uint8_t)0
#define CAN_DATA_SIZE 8    // Number of data bytes in a CAN packet

uint8_t* raw1;
uint8_t* raw2;
uint8_t* raw3;
uint8_t* raw4;
uint8_t* raw5;
uint8_t* raw6;


bool first_reading = true;

Protocentral_ADS1220 ads1;
Protocentral_ADS1220 ads2;
Protocentral_ADS1220 ads3;

extern UART_HandleTypeDef huart2;

extern SPI_HandleTypeDef hspi1;

extern DMA_HandleTypeDef hdma_usart2_tx;

extern FDCAN_HandleTypeDef hfdcan1;

int cnt1,cnt2,cnt3,cnt4,cnt5,cnt6;
uint32_t reading_cnt = 0;

int alt_main()
{
	/* Initialization */

	ads1.begin(GPIOA, GPIO_PIN_2, GPIOA, GPIO_PIN_9);
	ads2.begin(GPIOA, GPIO_PIN_3, GPIOB, GPIO_PIN_0);
	ads3.begin(GPIOA, GPIO_PIN_4, GPIOA, GPIO_PIN_8);

	ads1.set_OperationMode(MODE_TURBO);
	ads2.set_OperationMode(MODE_TURBO);
	ads3.set_OperationMode(MODE_TURBO);

	ads1.set_data_rate(DR_1000SPS);
	ads2.set_data_rate(DR_1000SPS);
	ads3.set_data_rate(DR_1000SPS);

	ads1.set_pga_gain(PGA_GAIN_128);
	ads2.set_pga_gain(PGA_GAIN_128);
	ads3.set_pga_gain(PGA_GAIN_128);

	ads1.set_conv_mode_single_shot();
	ads2.set_conv_mode_single_shot();
	ads3.set_conv_mode_single_shot();

	cnt1 = 0;
	cnt2 = 0;
	cnt3 = 0;
	cnt4 = 0;
	cnt5 = 0;
	cnt6 = 0;

	while (1)
	{


	}
}


int serial_cnt = 0;

void main_1KHz_interrupt()
{

	ads1.select_mux_channels(MUX_AIN0_AIN1);
	ads1.Start_SingleShot_Conv();

	ads2.select_mux_channels(MUX_AIN0_AIN1);
	ads2.Start_SingleShot_Conv();

	ads3.select_mux_channels(MUX_AIN0_AIN1);
	ads3.Start_SingleShot_Conv();

	usleep(550);
	raw2 = ads1.Read_Data_Immediate();
	raw4 = ads2.Read_Data_Immediate();
	raw6 = ads3.Read_Data_Immediate();

	ads1.select_mux_channels(MUX_AIN3_AIN2);
	ads1.Start_SingleShot_Conv();

	ads2.select_mux_channels(MUX_AIN3_AIN2);
	ads2.Start_SingleShot_Conv();

	ads3.select_mux_channels(MUX_AIN3_AIN2);
	ads3.Start_SingleShot_Conv();

	usleep(550);

	raw1 = ads1.Read_Data_Immediate();
	raw3 = ads2.Read_Data_Immediate();
	raw5 = ads3.Read_Data_Immediate();

	// Prepare the first CAN packet with the first 4 uint16_t values
	FDCAN_TxHeaderTypeDef txHeader;

	txHeader.Identifier = CAN_MASTER_ID;
	txHeader.IdType = FDCAN_STANDARD_ID;
	txHeader.TxFrameType = FDCAN_DATA_FRAME;
	txHeader.DataLength = FDCAN_DLC_BYTES_8;
	txHeader.ErrorStateIndicator = FDCAN_ESI_ACTIVE;
	txHeader.BitRateSwitch = FDCAN_BRS_OFF;
	txHeader.FDFormat = FDCAN_CLASSIC_CAN;
	txHeader.TxEventFifoControl = FDCAN_NO_TX_EVENTS;
	txHeader.MessageMarker = 0;

	uint8_t packet0[8]; // Packet 0 with 8 bytes
	uint8_t packet1[8]; // Packet 1 with 8 bytes
	uint8_t packet2[8]; // Packet 2 with 8 bytes

	packet0[0] = CAN_DEVICE_ID;
	packet0[1] = 0;
	packet0[2] = raw1[0];
	packet0[3] = raw1[1];
	packet0[4] = raw1[2];
	packet0[5] = raw2[0];
	packet0[6] = raw2[1];
	packet0[7] = raw2[2];

	packet1[0] = CAN_DEVICE_ID;
	packet1[1] = 1;
	packet1[2] = raw3[0];
	packet1[3] = raw3[1];
	packet1[4] = raw3[2];
	packet1[5] = raw4[0];
	packet1[6] = raw4[1];
	packet1[7] = raw4[2];

	packet2[0] = CAN_DEVICE_ID;
	packet2[1] = 2;
	packet2[2] = raw5[0];
	packet2[3] = raw5[1];
	packet2[4] = raw5[2];
	packet2[5] = raw6[0];
	packet2[6] = raw6[1];
	packet2[7] = raw6[2];


	HAL_FDCAN_AddMessageToTxFifoQ(&hfdcan1, &txHeader, packet0);
	usleep(130);
	HAL_FDCAN_AddMessageToTxFifoQ(&hfdcan1, &txHeader, packet1);
	usleep(130);
	HAL_FDCAN_AddMessageToTxFifoQ(&hfdcan1, &txHeader, packet2);
	usleep(130);

}

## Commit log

2023-06-07 in progress. needs silkscreen and gpio headers
    [Satyrr_six_loadcell_pcb.brd, Satyrr_six_loadcell_pcb.sch]
2023-06-07 board finished, ready for design review
    [Satyrr_six_loadcell_pcb.brd, Satyrr_six_loadcell_pcb.sch]
2023-06-14 schemetic design review complete
    [Satyrr_six_loadcell_pcb.brd, Satyrr_six_loadcell_pcb.sch]
2023-06-14 Full review complete, ready to order
    [Satyrr_six_loadcell_pcb.brd]
2023-06-14 added 3d model
    [Satyrr_6_loadcell_PCB.SLDPRT]
2023-06-14 updated 3d model
    [Satyrr_6_loadcell_PCB.SLDPRT]
2023-06-14 added BOM
    [Satyrr_six_loadcell_pcb_BOM.csv, Satyrr_six_loadcell_pcb_BOM.xlsx]
2023-06-16 fixed silkscreen
    [Satyrr_six_loadcell_pcb.brd]
2023-10-02 updated readme photos
    [Satyrr_6_loadcell_PCB.SLDPRT]

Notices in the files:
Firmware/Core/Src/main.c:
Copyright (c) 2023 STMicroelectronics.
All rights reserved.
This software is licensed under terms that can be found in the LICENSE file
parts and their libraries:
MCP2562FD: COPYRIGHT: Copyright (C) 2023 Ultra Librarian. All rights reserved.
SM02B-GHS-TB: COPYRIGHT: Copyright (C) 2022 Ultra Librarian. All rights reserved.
